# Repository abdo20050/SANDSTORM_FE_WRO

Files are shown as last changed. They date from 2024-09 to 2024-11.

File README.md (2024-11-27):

# SANDSTORM_FE_WRO

Official SANDSTORM's future engineers repo for WRO. Here is our GitHub Documentation. You can navigate through it using the folder names:
- **Code** contains the main program and the testing program.
- **Schemes** includes journals, photos of CAD files, BOM, diagrams, and other documents.
- **Videos** has YouTube links for the trials.
- **ImagesV** contains photos of the prototypes, and vehicle parts
- **ImagesT** contains photos of the team members, logo, and our journey

# Hello, we are Team SANDSTORM!

We’re excited to introduce our robot for this year’s competition. You can check out a video of the robot in action here: [YouTube Video Link].

Additionally, all of our source code and design documentation can be found on our [GitHub repository](https://github.com/abdo20050/SANDSTORM_FE_WRO/tree/main.)

# Strategy:

Our robot is equipped with a webcam that handles multiple tasks, making the design more cost-efficient by reducing the need for additional sensors. The webcam detects the blue and orange lines to track the number of laps completed and determine whether the robot is moving clockwise or counterclockwise. It also identifies black walls to avoid collisions and reverse if necessary.

For the obstacle challenge, the webcam continues its primary functions and additionally detects red and green traffic signals to decide the direction the robot should take. The webcam is also used to adjust the calibration to accommodate different lighting conditions. Overall, the robot relies entirely on the webcam for all tasks in the challenge.

# Overview of Our Robot Design:

Our robot is powered by a robust **6 lithium battery** setup, providing stable power to all components, including the motors and the processing unit. The robot is built on a custom-designed, **3D-printed chassis**, optimized for durability and lightweight maneuverability.

At the heart of our system is the **Raspberry Pi 5**, which controls motor movements and processes real-time video for navigation and obstacle avoidance. The **webcam**, connected directly to the Raspberry Pi, captures live footage, enabling the robot to make intelligent decisions on the field.

# Motor and Steering Control:

- **Drive System**: The robot uses a **T-shaped 6V DC motor** to power the rear wheels, ensuring steady forward and backward motion.
- **Steering**: The front wheels are controlled by an **MG995 servo motor**, allowing precise control for both soft and hard turns, depending on the situation.

The rear-wheel drive is managed by an **L298N H-Bridge**, which mediates between the motor and the Raspberry Pi, efficiently controlling both speed and direction.

# Vision and Obstacle Detection:

For object detection, lane following, and traffic signal identification, the robot relies on a **webcam** mounted on the chassis. This camera sends real-time video to the Raspberry Pi for processing, allowing the robot to detect obstacles and adjust its direction accordingly.

# Tracking Progress:

To track movement and ensure accurate lap completion, we’ve incorporated an **MPU6050 IMU**. This sensor measures the robot’s orientation and movement, ensuring the robot completes the required laps and maintains balance during turns.

# User Feedback and Monitoring:

We tested the robot through practice laps and test drives to ensure that balance, accuracy, and precision are on point. This allowed us to monitor the robot’s performance during the challenge and make adjustments as necessary.

# Key Components at a Glance:

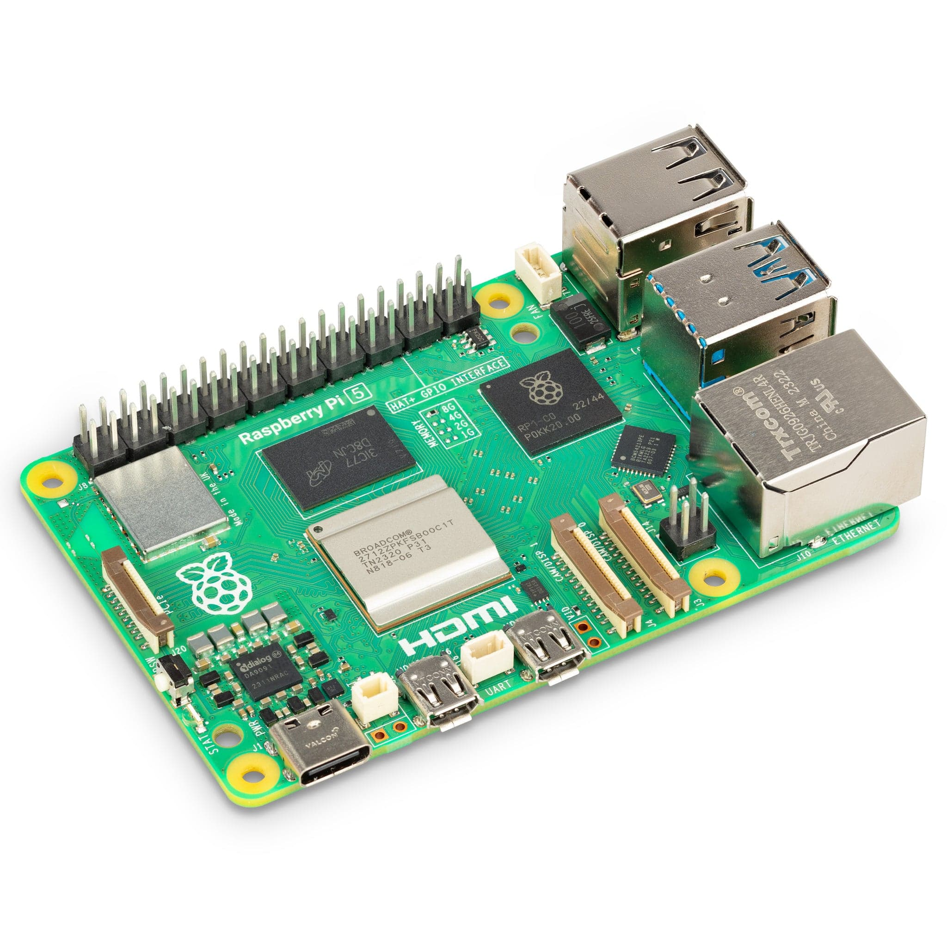
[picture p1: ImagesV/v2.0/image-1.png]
Raspberry Pi 5 – The main controller for processing inputs and controlling the motors and camera.


`Raspberry Pi 5 – The main controller for processing inputs and controlling the motors and camera.`

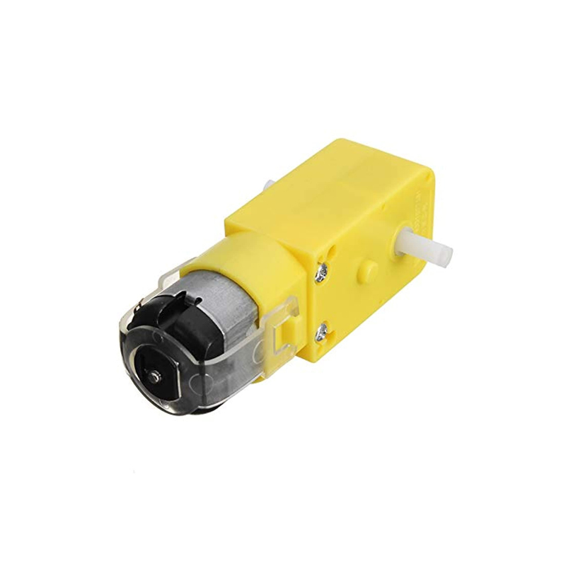
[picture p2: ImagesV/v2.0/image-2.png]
6V T-Shaped DC Motor – Drives the rear wheels, enabling smooth forward and backward motion.


`6V T-Shaped DC Motor – Drives the rear wheels, enabling smooth forward and backward motion.`

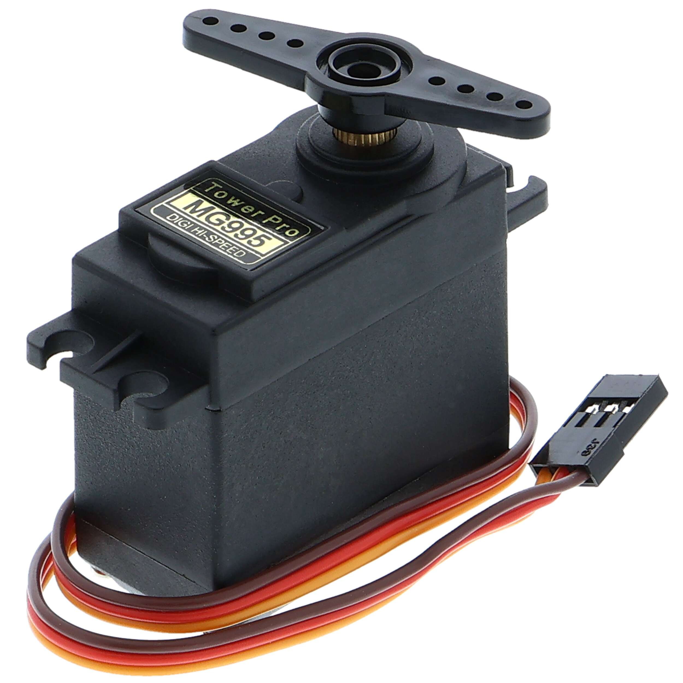
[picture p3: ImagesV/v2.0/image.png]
MG995 Servo Motor – Controls the front wheels for steering.


`MG995 Servo Motor – Controls the front wheels for steering.`

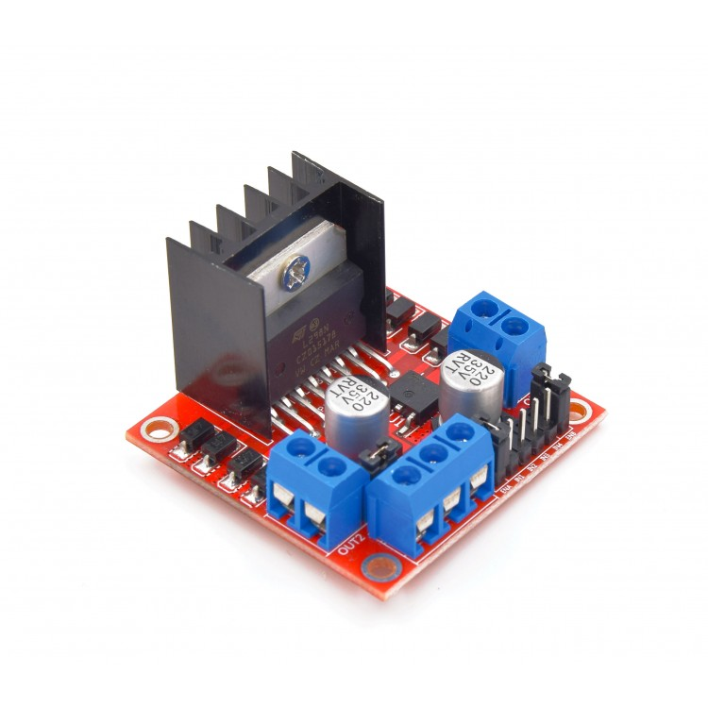
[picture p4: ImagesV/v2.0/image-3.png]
L298N H-Bridge – Motor driver that controls the speed and direction of the DC motor.


`L298N H-Bridge – Motor driver that controls the speed and direction of the DC motor.`

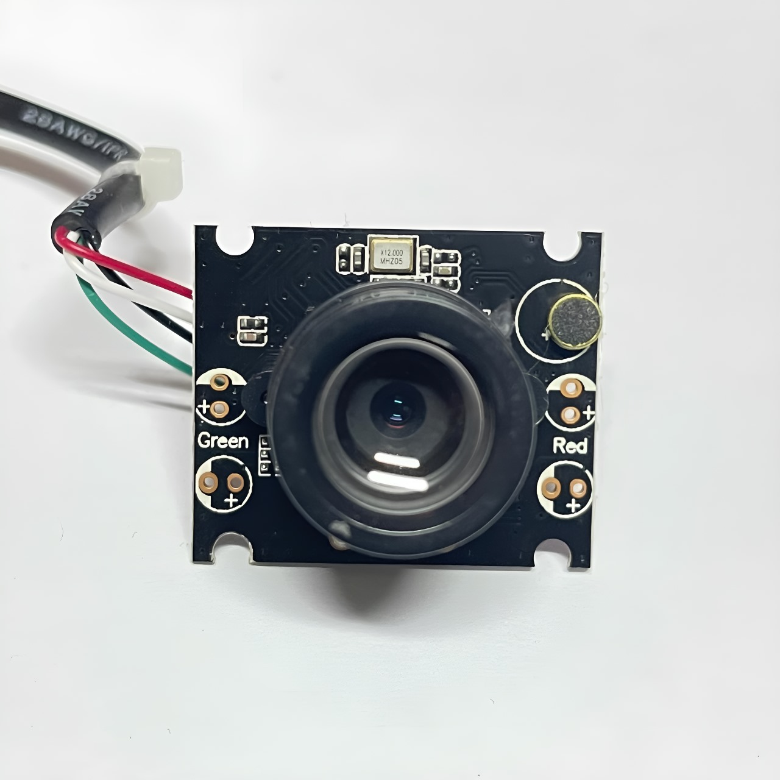
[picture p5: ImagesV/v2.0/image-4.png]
Webcam – Captures live video for real-time object detection and lane following.


`Webcam – Captures live video for real-time object detection and lane following.`

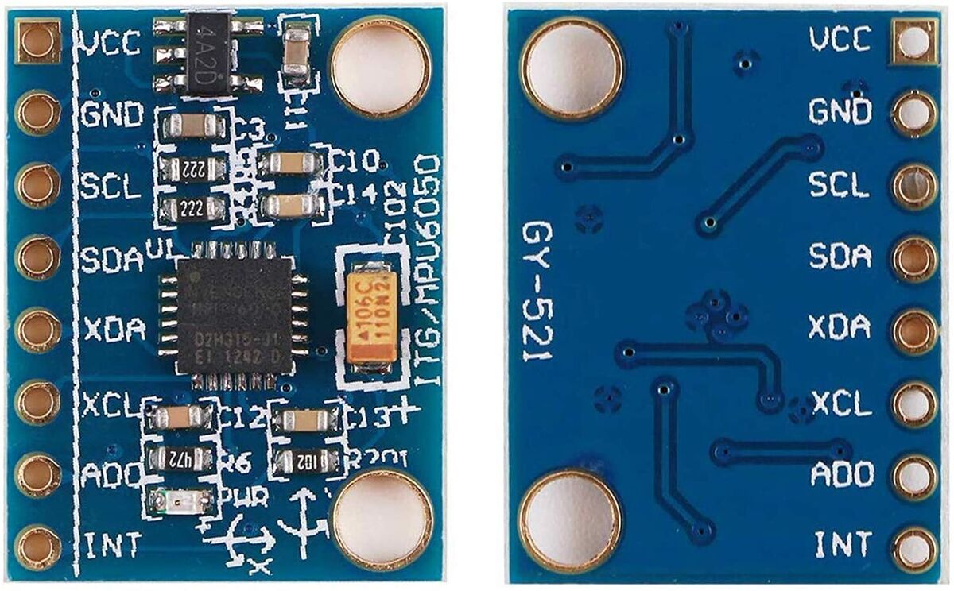
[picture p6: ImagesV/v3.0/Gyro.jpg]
GY-521, MPU6050 – Tracks orientation and movement to ensure accurate lap counting (we removed it temporarily for v2.0, now its back on v3,0).


`MPU6050 IMU – Tracks orientation and movement to ensure accurate lap counting (we removed it temporarily).`

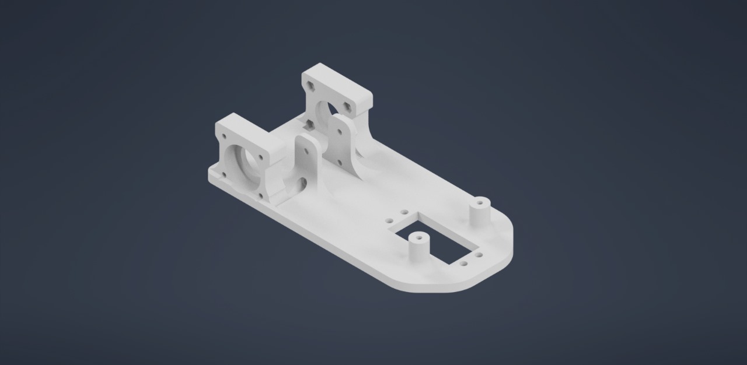
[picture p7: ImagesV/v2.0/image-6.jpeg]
Custom 3D-Printed Chassis – Lightweight and durable, designed to securely hold all components.


`Custom 3D-Printed Chassis – Lightweight and durable, designed to securely hold all components.`

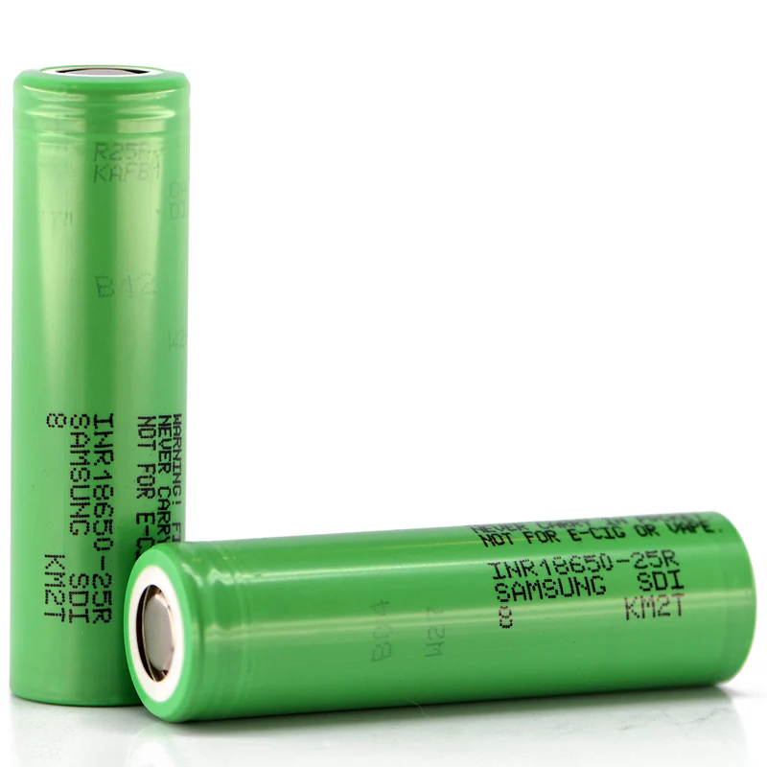
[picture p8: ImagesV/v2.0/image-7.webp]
Power Supply – Powered by 6 lithium batteries, ensuring reliable energy for all components.


`Power Supply – Powered by 6 lithium batteries, ensuring reliable energy for all components.`

---

This is the robot we’ve designed and built to tackle this year's challenge! For more details on how it works and how we approached the problem, feel free to explore the source code and documentation on our [GitHub](https://github.com/abdo20050/SANDSTORM_FE_WRO/tree/main.)

Additionally, here’s a document with more information: [Google Doc Link](https://docs.google.com/document/d/1cCJuQa-ENeIftLrWq0BU486fTGV7BMiAK_tZXONVTxw/edit?usp=sharing) (please request access or ask a team member for details).

Thank you for following our journey! Let us know if you have any questions or feedback.

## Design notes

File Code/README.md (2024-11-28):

This file has the used codes for the robot
# v1.0:
- Code.ino: the code for the aurduino in the challenges (used before, refer to the engineering journal)
- US_TESTER.ino: the arduino code for testing the ultrasonic sensor
# v2.0:
- Has some of the main codes that were used mainly, some other codes weren't available for here, however it is similar to v3.0
# v3.0:
- Has most codes, if you check deep enough you'll find some funny prompts :). **THE CODES AREN'T FULL, TO AVOID ANY STEALING, SOME OF THEM AREN'T UPLOADED HERE, ONLY ON THE ROBOT**

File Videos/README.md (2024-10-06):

This folder has a videos during the journey.
# v1.0
- Links.md: has 2 links which were submitted in the local qualifiers 
# v2.0: Folder that has videos about the second version of the robot:
- TestDrive.MOV: A video of the first test drive to check if the motors are working, weight is balanced (it doesn't topple), circuit is working
- Links.md: has 2 links which were submitted in the national qualifiers

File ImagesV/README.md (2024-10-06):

This folder contains the images of all sides of the robot.
# v1.0:
 has the first robot, a prototype, used for the regional qualifiers
# v2.0:
 has the second robot, used for the national qualifiers

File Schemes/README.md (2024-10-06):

This folder has the Bill Of Materials, two 3D printing files that were planned to be used but failed, A diagram for the components. 
# v1.0:
 for the arduino version (old)
# v2.0:
 for the raspberry pi version (newer)

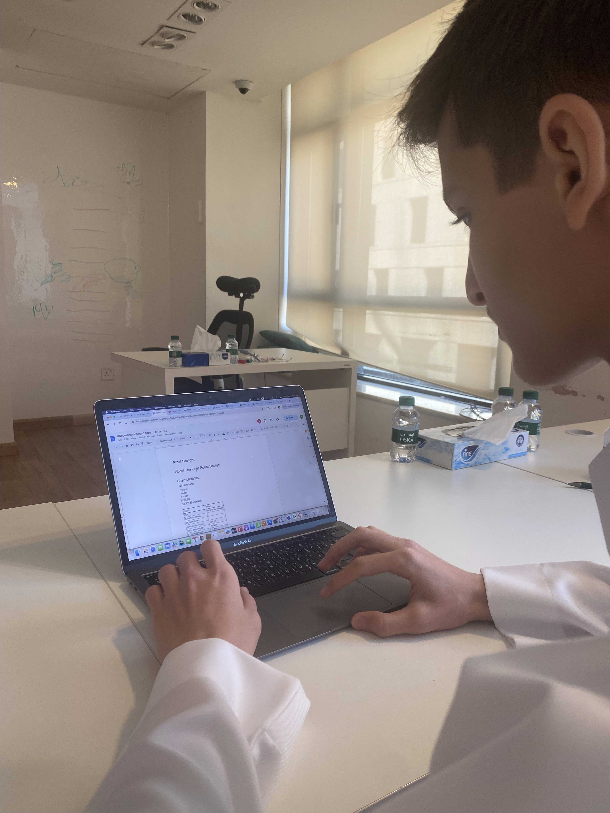
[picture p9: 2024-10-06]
ImagesT/Working2.jpg

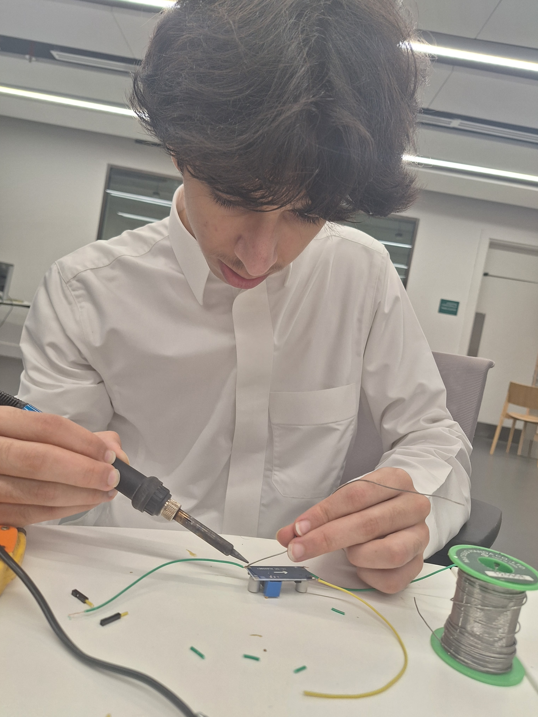
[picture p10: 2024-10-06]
ImagesT/Working1.jpg

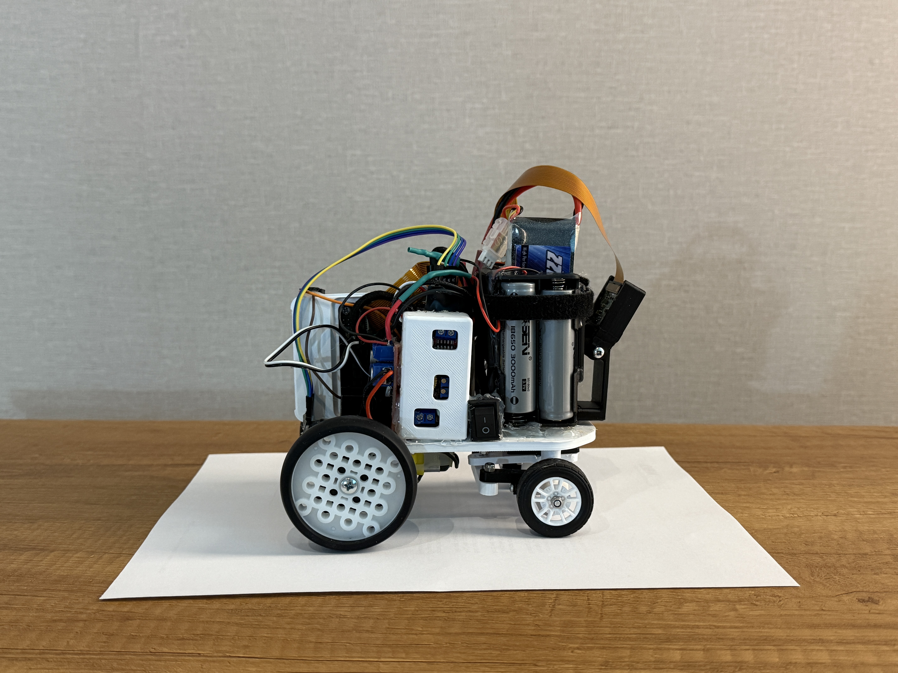
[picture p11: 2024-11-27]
ImagesV/v3.0/Right_3.0.JPG

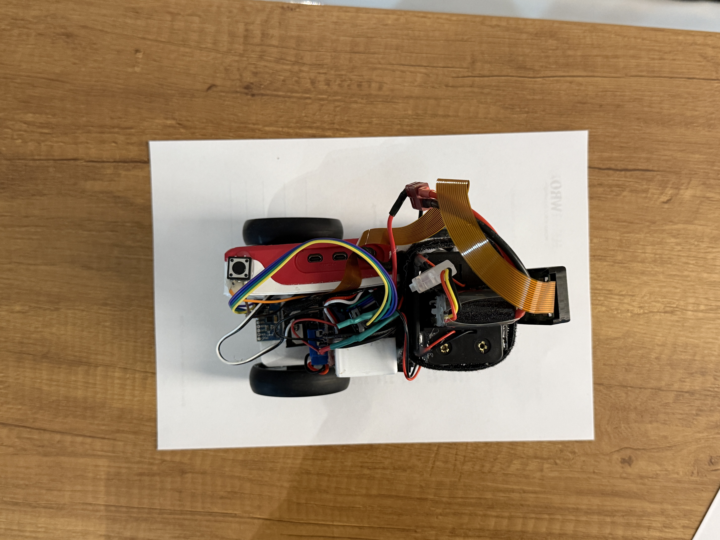
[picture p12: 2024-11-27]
ImagesV/v3.0/Top_3.0.JPG

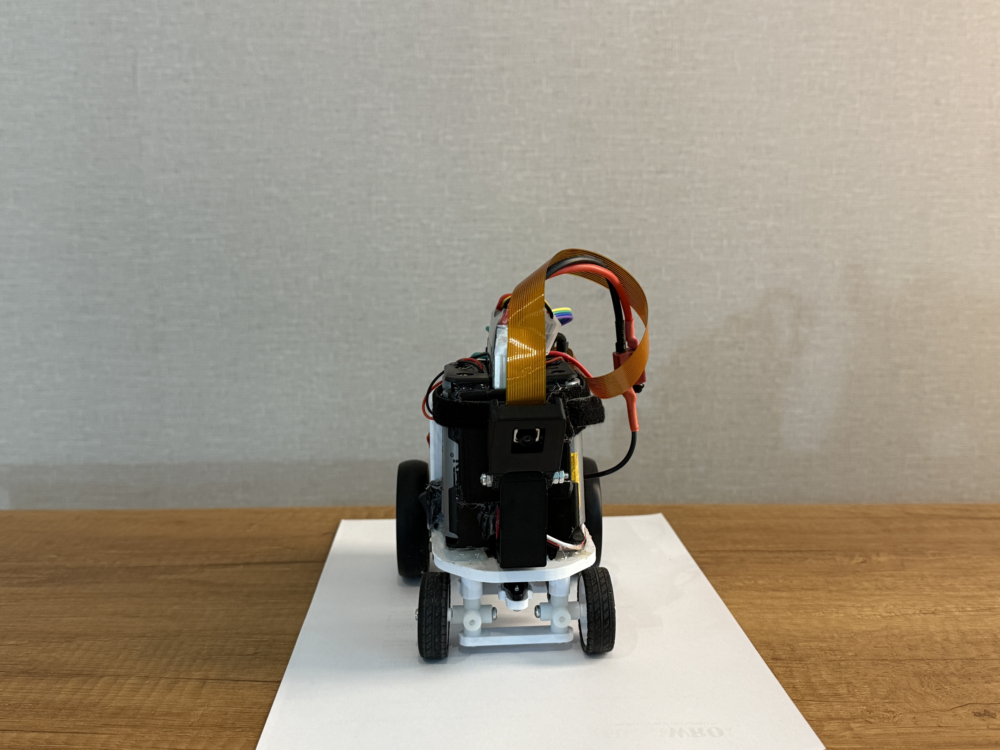
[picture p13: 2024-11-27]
ImagesV/v3.0/Front_3.0.JPG

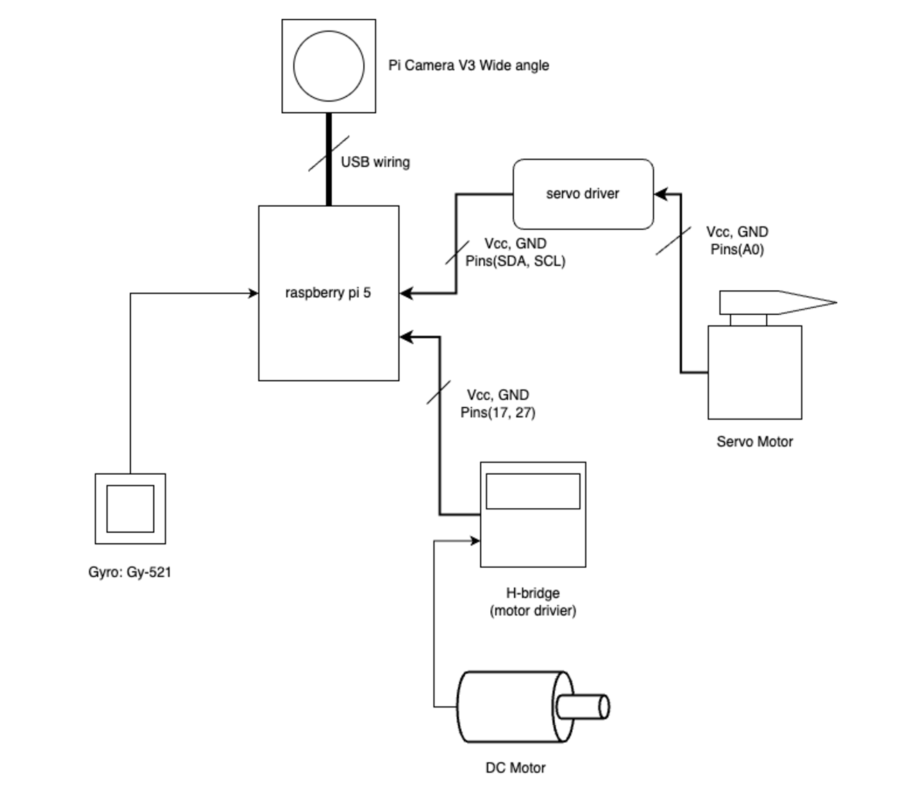
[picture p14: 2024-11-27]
Schemes/v3.0/v3.0 Circuit Diagram.png

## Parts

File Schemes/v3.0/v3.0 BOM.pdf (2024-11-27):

Object: | Number of pieces: | Price Per Piece: | Total price:
Pla+ | 500 gram | 100 SAR Per Kilo | 50 SAR
Small Front Wheels | 2 | 3 SAR | 6 SAR
Big Back Wheels | 2 | 5 SAR | 10 SAR
Dc motor: 6v, Tshape | 1 | 10 SAR | 10 SAR
Servo motor: mgDS 3240 | 1 | 20 SAR | 20 SAR
Lithium Batteries | 6 | 20 SAR | 120 SAR
Raspberry pi 5 | 1 | 450 SAR | 450 SAR
Step Down transformer: DC | 1 | 10 SAR | 10 SAR
Hbridge: L298N | 1 | 20 SAR | 20 SAR
Battery Case | 2 | 3 SAR | 6 SAR
Screw & Nut Kit: | 1 | 30 SAR | 30 SAR
PiCamera v3 wide angle | 1 | 100 SAR | 100 SAR
Servo Driver | 1 | 25 SAR | 25 SAR
Kit of Wires | 1 | 10 SAR | 10 SAR
Gyro: Gy-521 | 1 | 48 SAR | 48 SAR
Total amount: | | | 915 SAR

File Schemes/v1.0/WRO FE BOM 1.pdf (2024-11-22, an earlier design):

Prototype:
Object: | Price:
2 Big Back wheels | 5 SAR
Battery | 150 SAR
IMU | 20 SAR
Pixy | 400 SAR
H bridge | 20 SAR
Structure | 300 SAR
DC Motor | 50 SAR
3 ultrasonic | 10 sar per sensor
Kit of wires | 20 SAR
LCD display | 35 SAR
2 small front wheels | 5 SAR
Arduino mega | 120 SAR
Servo | 25 SAR
Voltmeter | 15 SAR
Total amount: | 1195 SAR

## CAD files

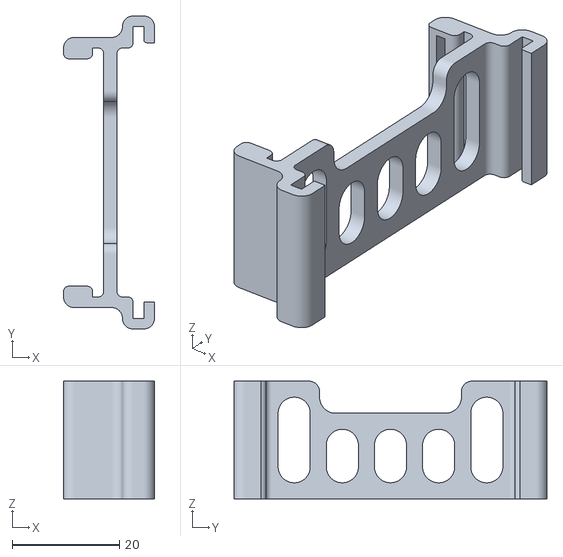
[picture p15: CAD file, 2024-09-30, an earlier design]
Schemes/v1.0/Failed_Des2.stl
17.0 x 58.5 x 22.0

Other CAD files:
Schemes/v1.0/Failed_Des1.stl

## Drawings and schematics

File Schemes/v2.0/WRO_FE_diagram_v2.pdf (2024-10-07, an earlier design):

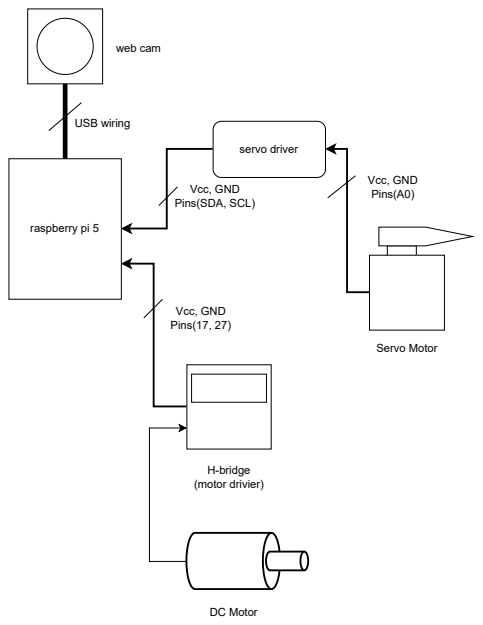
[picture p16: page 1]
raspberry pi 5; web cam; USB wiring; H-bridge (motor drivier); Vcc, GND Pins(17, 27); DC Motor; Servo Motor; servo driver; Vcc, GND Pins(A0)

Vcc, GND
Pins(SDA, SCL)

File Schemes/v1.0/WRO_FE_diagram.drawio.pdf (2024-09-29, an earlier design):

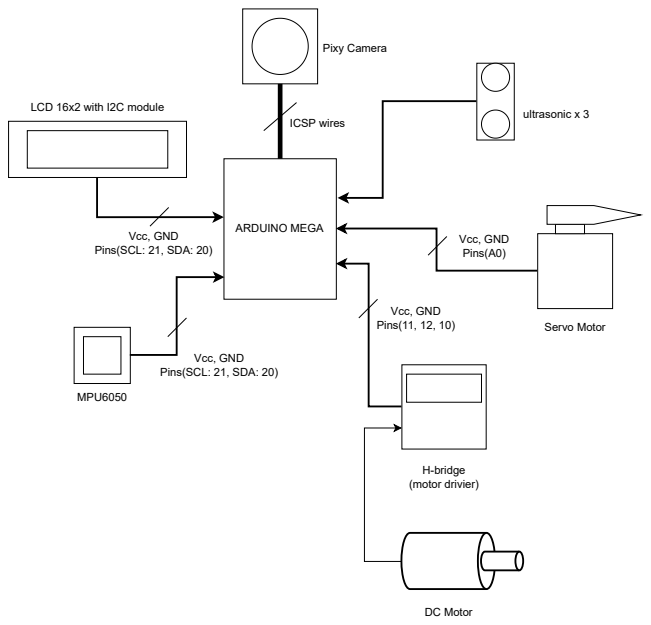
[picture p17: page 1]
ARDUINO MEGA; Pixy Camera; ICSP wires; ultrasonic x 3; MPU6050; H-bridge (motor drivier); Vcc, GND Pins(11, 12, 10); DC Motor; Servo Motor; Vcc, GND Pins(A0)

LCD 16x2 with I2C module

Vcc, GND
Pins(SCL: 21, SDA: 20)

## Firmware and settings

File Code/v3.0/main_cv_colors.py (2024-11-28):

import cv2
import numpy as np
from picamera2 import Picamera2
from process_frames_colors import *
from motor_controller import create_dc_motor
from servo_controller import create_servo
from MPUSensor_controller import create_mpu_sensor
import collections

import time

def _get_raw_rc_angle(mpu):
        """Get current raw angle from sensor."""
        sensor_data = mpu.get_sensor_data()
        if not sensor_data:
            print("no gyro data")
            return None
        yaw_angle_raw = sensor_data['gyro_angles'][2]
        yaw_angle_raw
        return yaw_angle_raw

def get_rc_angle(mpu):
        sensor_data = mpu.get_sensor_data()
        return sensor_data['yaw']

class stuck_checker:
    def __init__(self):
         pass
         self.currTime = time.time()
         self.similarity_start_time = 0
         self.previous_frame = None
    def frames_are_similar(self, frame1, frame2, threshold):
        if frame1 is None or frame2 is None:
            return False
        # Convert to grayscale for simpler comparison
        gray1 = cv2.cvtColor(frame1, cv2.COLOR_BGR2GRAY)
        gray2 = cv2.cvtColor(frame2, cv2.COLOR_BGR2GRAY)

        # Compute structural similarity
        difference = cv2.absdiff(gray1, gray2)
        _, diff_thresh = cv2.threshold(difference, 25, 255, cv2.THRESH_BINARY)

        # Calculate the ratio of non-difference pixels
        non_zero_count = np.count_nonzero(diff_thresh)
        total_pixels = frame1.shape[0] * frame1.shape[1]
        similarity_ratio = (total_pixels - non_zero_count) / total_pixels

        return similarity_ratio >= threshold
    
    def check_if_stuck( self, frame, similarity_threshold = 0.9, similarity_duration = 3):
        # Check for frame similarity over time (car is stuck)
        # print('in check')
        self.currTime = time.time()
        if self.previous_frame is None:
             self.previous_frame = frame.copy()
             return False
        
        # print("HHHHH")
        if self.frames_are_similar(self.previous_frame, frame, threshold=similarity_threshold):
            if self.similarity_start_time == 0:
                self.similarity_start_time = self.currTime
            elif self.currTime - self.similarity_start_time >= similarity_duration :
                print("stuck")
                
                self.similarity_start_time = 0  # Reset the timer
                return True
            else:
                pass
                # print("checking stuck..")
        else:
            # Reset similarity timer if the frames are not similar
            self.similarity_start_time = 0
            self.previous_frame = frame.copy()
            return False
        
    

def main():
    motor = create_dc_motor()
    servo = create_servo(channel=0, reverse_angle=True, max_angle=45)
    mpu = create_mpu_sensor()
    servo.center()
    initial_point = -1
    prev_wall_point = -1
    counter = 0
    prev_time_counter = time.time()
    prev_time_SteerLock = time.time()
    lab_count = 0
    start_counter = False
    num_points_avg = 10 # How many points from the trace to avg
    steerLock_duration = 0
    stuck_checker_obj = stuck_checker()
    steer_angle = 0
    steer_angle_buffer = collections.deque(maxlen=3) #Increase this for smoother steering but too much will cause some steer delay
    default_speed = 0.7
    run_speed = default_speed
    try:
        while True:
            rc_angle = get_rc_angle(mpu)
            curr_time = time.time()
            frame = picam2.capture_array()
            frame = cv2.rotate(frame, cv2.ROTATE_180)
            offset_steer, wall_point, comp_img, flag = process_frame(frame.copy(), num_points_avg)
            cv2.imshow("preview", comp_img)

            if cv2.waitKey(1) & 0xFF == ord('q'):
                break
            
                 
            if steerLock_duration:
                 if curr_time - prev_time_SteerLock < steerLock_duration:
                    continue 
                 else:
                    motor.set_speed(0)
                    steerLock_duration = 0
            
            if stuck_checker_obj.check_if_stuck(frame):
                steerLock_duration = 4 #seconds to go backward
                prev_time_SteerLock = curr_time
                steer_angle = -steer_angle
                servo.set_angle(0)
                steer_angle_buffer.clear()
                if run_speed:
                    motor.set_speed(-0.5)
                continue
            if len(flag) > 0:
                print(flag)
                if "hard backward" in flag:
                    steerLock_duration = 1.4 #seconds to go backward
                    prev_time_SteerLock = curr_time
                    motor.set_speed(-0.5)
                    if 'green' in flag:
                        servo.set_angle(-20) # backward with right steer
                    elif 'red' in flag:
                        servo.set_angle(20) # backward with left steer
                    steer_angle_buffer.clear()
                    continue

                elif "hard turn" in flag:
                    steerLock_duration = 0.8 #seconds to go backward
                    if run_speed:
                        run_speed = 0.7
                        motor.set_speed(run_speed)
                    if "green" in flag:
                        steer_angle = servo.max_angle
                    elif "red" in flag:
                        steer_angle = -servo.max_angle
                    servo.set_angle(steer_angle)

                    continue
            else:
                if run_speed:
                    run_speed = default_speed

            max_offset = 40.0
            offset_steer = min(max_offset, max(-max_offset, offset_steer))
            steer_ratio = offset_steer / max_offset
            steer_angle = int(steer_ratio*servo.max_angle)
            steer_angle_buffer.append(steer_angle)
            smoothed_steering_angle  = sum(steer_angle_buffer)/len(steer_angle_buffer)
            # print(smoothed_steering_angle)
            servo.set_angle(smoothed_steering_angle)
            motor.set_speed(run_speed)
            
            # counting labs section
            if wall_point is not None:
                if initial_point < 0:
                        prev_time_counter = curr_time
                        initial_point = wall_point[1] + 10
                        # prev_wall_point = 1000
                if curr_time - prev_time_counter > 10:
                    
                    if abs(rc_angle) < 10:
                        print(rc_angle)
                        print(wall_point)
                        if wall_point[1] > 30:
                            if wall_point[1] >= initial_point and prev_wall_point < initial_point:
                                if start_counter:
                                    counter+=1
                                    print("counter: ", counter)
                                    if counter == 3:
                                        motor.set_speed(-0.8)
                                        time.sleep(0.2)
                                        break
                                    prev_time_counter = curr_time
                        prev_wall_point = wall_point[1]
                    else:
                         start_counter = True
                         prev_wall_point = 0
        
    finally:
        picam2.stop()
        cv2.destroyAllWindows()
        servo.center()
        # servo.unlock()
        motor.stop()
        

if __name__ == "__main__":
    # Initialize Picamera2
    picam2 = Picamera2()
    RESIZE_FACTOR = 1
    # picam2.sensor_mode = 4
    #2304 x 1296-PC1B
    cam_res = (2304 // RESIZE_FACTOR, 1296 // RESIZE_FACTOR)

    video_config = picam2.create_video_configuration(raw={"size": cam_res, "format" : 'SGBRG10'}, main = {"size":(2304//10, 1296//10)})
    picam2.configure(video_config)
    picam2.start()

    load_hsv_from_json()
    main()

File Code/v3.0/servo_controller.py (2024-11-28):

import time
from adafruit_servokit import ServoKit

class ServoController:
    def __init__(self, channel=0, min_pulse=1000, max_pulse=2000, reverse_angle=False, max_angle=90):
        # Initialize ServoKit
        self.kit = ServoKit(channels=16)
        self.channel = channel
        self.angle_fix = -5
        
        # Set up the servo
        self.max_angle = max_angle
        # self.kit.servo[self.channel].set_pulse_width_range(min_pulse, max_pulse)
        self.reverse_factor = -1 if reverse_angle else 1

    def set_angle(self, angle):
        """Set the servo to a specific angle (-90 to 90 degrees)."""
        if -90 <= angle <= 90:
            angle += self.angle_fix
            # angle += 90
            mapped_angle = (self.reverse_factor * angle) + 90
            self.kit.servo[self.channel].angle = mapped_angle
        else:
            raise ValueError("Angle must be between -90 and 90 degrees")

    def sweep(self, start=-90, end=90, step=5, delay=0.1):
        """Perform a sweep from start to end angle."""
        for angle in range(start, end + 1, step):
            self.set_angle(angle)
            time.sleep(delay)

    def center(self):
        """Center the servo (set to 0 degrees)."""
        self.set_angle(0)

def create_servo(channel=0, min_pulse=1000, max_pulse=2000, reverse_angle=False, max_angle=90):
    """Create and return a ServoController instance."""
    return ServoController(channel, min_pulse, max_pulse, reverse_angle, max_angle)

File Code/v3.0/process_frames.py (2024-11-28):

import cv2
import numpy as np
from picamera2 import Picamera2


def display_live_window(image, window_name="Live Tracking"):
    """Utility function to display images in OpenCV window."""
    cv2.imshow(window_name, image)
    cv2.waitKey(1)  # 1 ms wait to allow OpenCV to process the window

def find_bottommost_contour(contours, image_height):
    """
    Find the contour closest to the bottom of the image.

    :param contours: List of contours.
    :param image_height: Height of the image.
    :return: The contour closest to the bottom.
    """
    max_bottom = 0
    bottommost_contour = None

    for contour in contours:
        # Find the bottommost point of the contour
        bottom_point = max(contour, key=lambda point: point[0][1])
        bottom_y = bottom_point[0][1]
        
        # Update the closest contour if this one is lower
        if bottom_y > max_bottom:
            max_bottom = bottom_y
            bottommost_contour = contour

    return bottommost_contour
def generate_path(filtered_track):
    """
    Generate a path based on the centerline of the filtered track.

    :param filtered_track: Binary image with the track in white pixels.
    :return: Path points [(x1, y1), (x2, y2), ...].
    """
    height, width = filtered_track.shape
    path_points = []

    for y in range(height):
        # Find white pixels in the current row
        white_pixels = np.where(filtered_track[y, :] == 255)[0]
        if len(white_pixels) > 0:
            # Calculate the midpoint of the white pixels
            center_x = (white_pixels[0] + white_pixels[-1]) // 2
            path_points.append((center_x, y))

    return np.array(path_points)

def filter_path_points(path_points, smoothing_window=5, deviation_threshold=20):
    """
    Filter noisy path points using smoothing and deviation filtering.

    :param path_points: Array of (x, y) path points.
    :param smoothing_window: Size of the moving average smoothing window.
    :param deviation_threshold: Maximum allowable deviation from the fitted path.
    :return: Filtered path points.
    """
    np.array(path_points)
    # Separate x and y coordinates
    x_values = path_points[:, 0]
    y_values = path_points[:, 1]

    # Step 1: Moving Average Smoothing
    smooth_x_values = np.convolve(
        x_values, np.ones(smoothing_window) / smoothing_window, mode="same"
    )

    # Step 2: Fit a polynomial to the smoothed points
    fit = np.polyfit(y_values, smooth_x_values, deg=2)  # Quadratic fit
    fitted_x_values = np.polyval(fit, y_values)

    # Step 3: Remove points with large deviations
    deviations = np.abs(x_values - fitted_x_values)
    filtered_indices = deviations < deviation_threshold
    filtered_path_points = path_points[filtered_indices]

    return filtered_path_points

def process_frame(frame, num_points_avg):
    original = cv2.cvtColor(frame, cv2.COLOR_BGR2RGB)  # Convert to RGB for plt
    gray = cv2.cvtColor(frame, cv2.COLOR_BGR2GRAY)
    # Step 2: Filter Black Walls and Highlight White Track
    gray = cv2.GaussianBlur(gray, ksize=(5,5), sigmaX=10)
    _, white_mask = cv2.threshold(gray, 120, 255, cv2.THRESH_BINARY)  # White track
    _, black_mask = cv2.threshold(gray, 100, 255, cv2.THRESH_BINARY_INV)  # Black walls
    height, width = gray.shape

    inverted_black_mask = 255-np.array(black_mask)
    # contours, _ = cv2.findContours(white_mask, cv2.RETR_EXTERNAL, cv2.CHAIN_APPROX_SIMPLE)
    contours, _ = cv2.findContours(inverted_black_mask, cv2.RETR_EXTERNAL, cv2.CHAIN_APPROX_SIMPLE)
    largest_contour_index = max(range(len(contours)), key=lambda i: cv2.contourArea(contours[i]))
    filtered_track = np.zeros_like(gray)
    cv2.drawContours(filtered_track, contours, largest_contour_index, 255, thickness=cv2.FILLED)
    # Get the middle column of the image
    middle_x = width // 2
    middle_column = filtered_track[:, middle_x]

    # Find indices where the pixel value is white (255)
    white_indices = np.where(middle_column == 255)[0]
    wall_point = None
    if white_indices.size > 0:
        # Get the lowest y-value (maximum index since y increases downward in images)
        lowest_y = white_indices[0]
        wall_point = (middle_x, lowest_y)
        # print(f"Lowest black point in the middle column: {wall_point}")
    else:
        print("No black pixels found in the middle column.")
    roi = np.zeros_like(gray)
    lower_region = int(height * 0.3)  # Adjust the starting point of the lower ROI
    higher_region = int(height * 0.7)
    roi[lower_region:higher_region, :] = 255  # Keep only the lower region
    filtered_track = cv2.bitwise_and(filtered_track, roi)
    # Iterate through each column
    for x in range(width):
        # Flag to indicate if a black pixel has been encountered in the column
        black_found = False
        for y in range(int(height*0.2),height):
            if filtered_track[y, x] == 0:  # Black pixel encountered
                black_found = True
                break
            else:
                # Black out the current pixel in the white mask
                filtered_track[y, x] = 0    
    
    path_points = generate_path(filtered_track)
    try:
        pass
        path_points = filter_path_points(path_points, smoothing_window=5, deviation_threshold=20) 
    except:
        pass

    for i in range(len(path_points) - 1):
        cv2.line(original, path_points[i], path_points[i + 1], (255, 0, 0), 2)

    try:
        offset_steer =  width//2 - int(np.mean(path_points[-num_points_avg: ,0]))
        # if start_path_point > height//2:
        #     # offset_steer = path_points[path_points[:,1]==77][0][0] - path_points[path_points[:,1]==50][0][0]
        # else:
        #     offset_steer = 0
    except:
        offset_steer = 0
    # print(offset_steer)

    cv2.line(original, 
            (width//2, height), 
            (width//2 - offset_steer, height*3//4), 
            (0,255,0), 2)  # Path line
    
    filtered_track_rgb = cv2.cvtColor(filtered_track, cv2.COLOR_GRAY2RGB)
    # Display all images in OpenCV window
    combined_image = np.hstack([original, filtered_track_rgb])
    # display_live_window(combined_image)
    return offset_steer, wall_point, combined_image
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

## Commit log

2024-10-06 Create 3D Chassis.jpeg
2024-10-06 National Finals
    [Failed_Des1.stl, Failed_Des2.stl]
2024-10-06 National stage
2024-10-07 Update and rename Code/calibration_v2.py to Code/v2/calibration_v2.py
2024-11-22 Adding pictures for the team after qualifying for the international stage
